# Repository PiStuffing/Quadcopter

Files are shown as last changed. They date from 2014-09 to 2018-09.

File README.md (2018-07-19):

Quadcopter
==========

Python project for an Raspberry Pi Autonomous Quadcopter Flight Controller

<a href="http://blog.pistuffing.co.uk/blog">Zoe flight</a>

Licensing
---------
<br />This work is licensed under a <a rel="license" href="http://creativecommons.org/licenses/by-nc-sa/4.0/">Creative Commons Attribution-NonCommercial-ShareAlike 4.0 International License</a>.

Index
-----
Documentation
<ul>
<li>README.md          - This file</li>
<li>LICENCE            - Usage definition</li>
<li>piDrones.pdf       - Documentation of piDrone details.</li>
</ul>
Code
<ul>
<li>piDrone            - Shell script driving qc.py with -O performance parameter
<li>qc.py              - Python wrapper allowing automatic use of the pre-compiled .pyc version of Quadcopter.py</li>
<li>Quadcopter.py      - Core flight controller code</li>
<li>RC.py              - Remote Control code</li>
</ul>
Flight plans
<ul>
<li>20s_hover_fp.csv   - Example simple flight plan CSV input file to hover a 1m</li>
<li>2m_square_fp.csv   - Example flight plan CSV input file to fly a 1m square 1m above the ground</li>
</ul>
Python libraries
<ul>
<li>RPIO.tgz           - clone of RPIO hardware PWM library (search GitHub for original)</li>
<li>smbus2.zip         - clone of I2C variount required for the RC joysticks (search GitHub for original)</li>
</ul>
PCBs
<ul>
<li>RPi0-PCB.brd       - Eagle board for Raspberry Pi 0 Quad</li>
<li>RPi3-PCB.brd       - Eagle board for Raspberry Pi 3 X8</li>
</ul>
Sensors
<ul>
<li>IMU_spec.pdf       - Invensense MPU-9250 specifications</li>
<li>GPS_spec.pdf       - u-blox NEO-M8T specification</li>
<li>Sweep_spec.pdf     - Scanse Sweep specification</li>
<li>LiDAR_spec.pdf     - Garmin LiDAR-Lite v3 specification</li>
<li>LiDARv3HP_spec.pdf - Garmin LiDAR-Lite v3HP specification</li>
<li>Joystick_spec.pdf  - Grayhill 67A specification</li>
</ul>

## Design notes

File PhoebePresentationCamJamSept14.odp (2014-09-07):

## Phoebe the Python Quadcopter

## Applications

- Professional Video
  - Countryfile
- Big Boys' Toys
  - Blooming Market
- Research Projects

## Demonstration

- Keep you expectations low!
  - 3 seconds take-off
  - 3 seconds hover
  - 3 seconds descent
  - autonomously
- Stand well back and be ready to run

## Hardware

- Props, Motors, ESCs, Frame off the shelf
- Raspberry Pi model A
- Custom PiBow + breadboard
- MPU6050 Sensor
- Velco, Blu-tack, Double-sided sticky tape

## Software

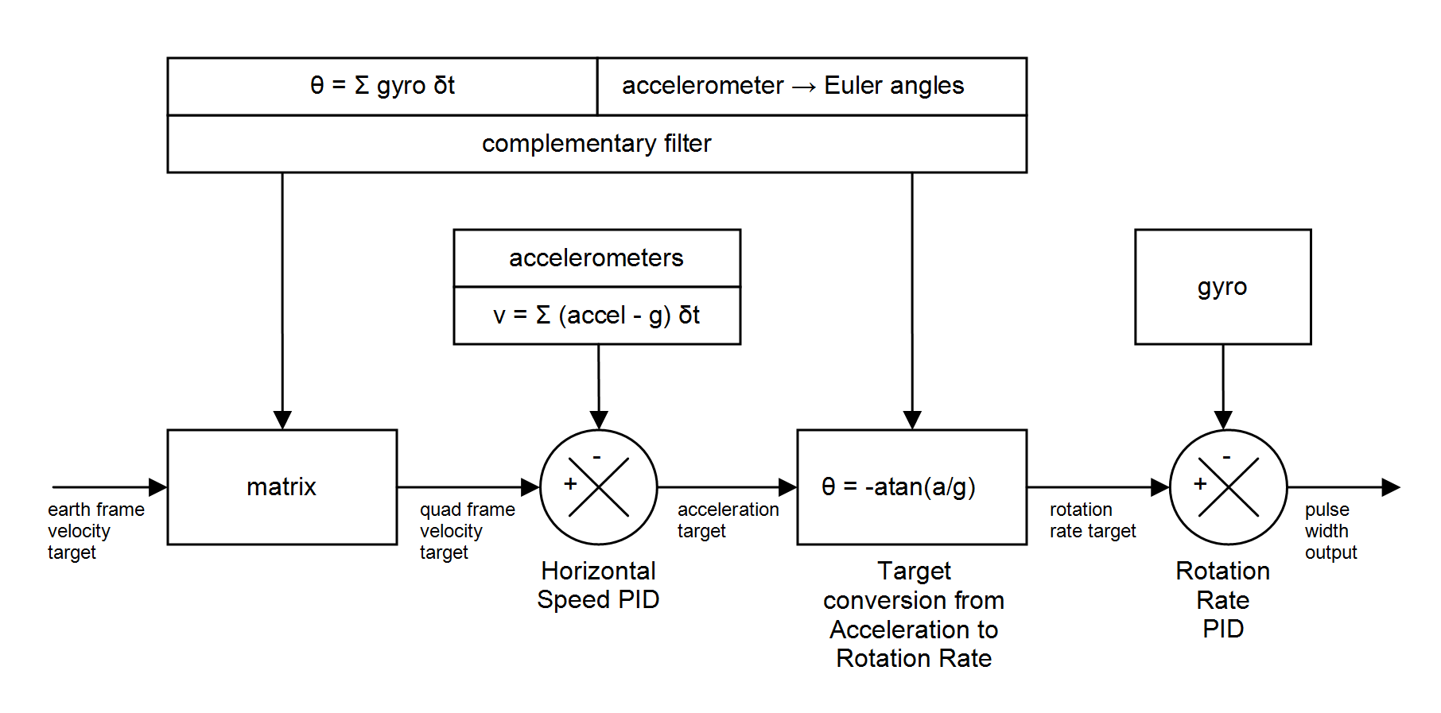
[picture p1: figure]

## Calibration

- Improve sensor accuracy
- Critical for velocity / gravity

## Performance

- Read sensors and integrate each loop
- Process results and feed @ 41Hz
- Performance 100Hz → 465Hz
  - I2C bus speed to 400kHz
  - MPU6050 data updates @ 1kHz
  - time.time()
  - GPIO interrupt
  - I2C read 1 x 14 bytes not 14 x 1 byte
  - GPU memory minimal
  - Code locked into memory

## What next?

- Physical rebuild
  - Frame
  - Motors, props, ESCs
- Sensors
  - Barometer / Altimeter
  - Magnetometer / Compass
  - GPS
- RaspiCam

## Any questions?

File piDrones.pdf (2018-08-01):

Master at https://github.com/PiStuffing/Quadcopter/blob/master/piDrones.pdf

# piDrones

## Version 1.0 – 1

## st August 2018

## Don’t Do It!

The aim of this documentation is to share details that could be interesting or useful for other projects. It lacks details about how to do your own DIY drone.

My target was to test the capabilities of me, a Raspberry Pi and python. I chose creating a piDrone not as a flying machine as such, but as an intellectual challenge requiring hardware, software and electronics.

My DIY piDrones has cost me £20k+ of research, development and testing over 6 years. Even building a DIY drone based on the instructions below will cost >£1.5k yet it supports (a little) less than a professional drone costing less than £1k.

If you want a flying machine, just buy a DJI Mavic or Spark and get out there flying.

However, if you want to know how flying machines work, read on…

## Internet Media

There are various links if you’re interested:

- pistuffing.co.uk has everything done over 6 years including non-drone projects and even non-Raspberry Pi projects
- pidrone.io/blog links to only drone posts
- pidrone.io/video links to only the videos
- pidrone.io/posts/xxx links to specific xxx posts for twitter
- vimeo.com/pistuffing covers all videos directly.

## Legal Constraint

The project, defined by the GitHub pistuffing/Quadcopter content, is for non-commercial usage. If you want to use this project commercially, contact me via andy@pistuffing.co.uk and let’s talk. After all, any financial compensation would be gratefully received!

Obviously, I’ll happily accept voluntary donations from anyone at http://blog.pistuffing.co.uk/donations/ 😊

## Raspberry Pis

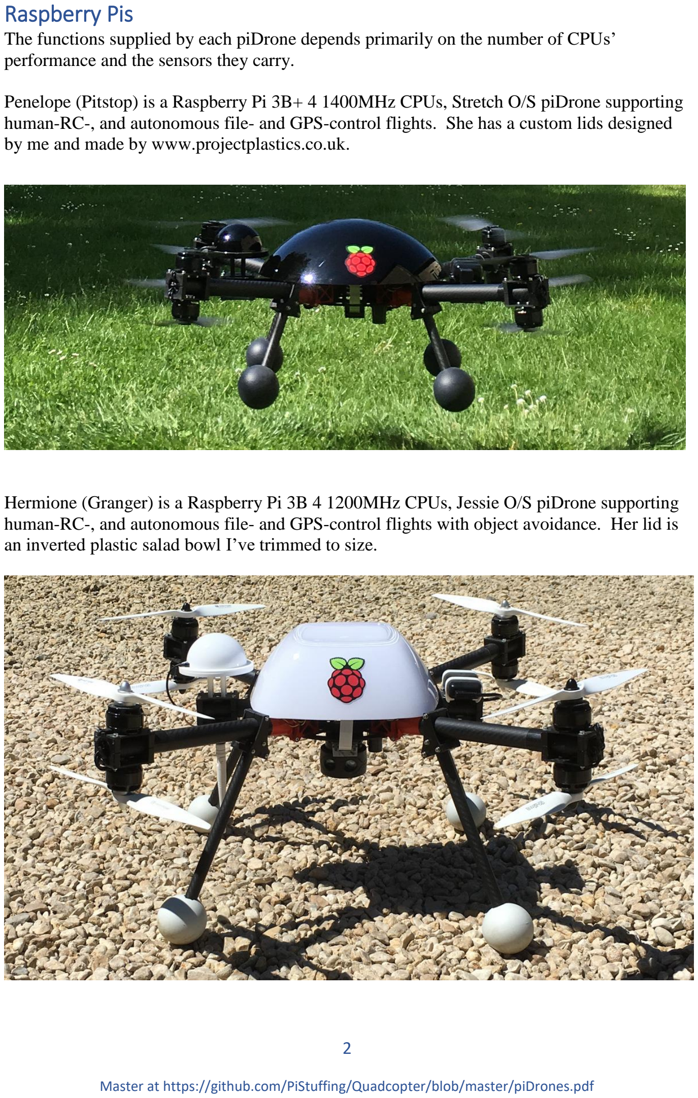
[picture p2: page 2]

The functions supplied by each piDrone depends primarily on the number of CPUs’ performance and the sensors they carry.

Penelope (Pitstop) is a Raspberry Pi 3B+ 4 1400MHz CPUs, Stretch O/S piDrone supporting human-RC-, and autonomous file- and GPS-control flights. She has a custom lids designed by me and made by www.projectplastics.co.uk.

Hermione (Granger) is a Raspberry Pi 3B 4 1200MHz CPUs, Jessie O/S piDrone supporting human-RC-, and autonomous file- and GPS-control flights with object avoidance. Her lid is an inverted plastic salad bowl I’ve trimmed to size.

Zoë (Johnny Ball’s daughter) is a Raspberry Pi0W single CPU, Stretch O/S piDrone supporting human-RC-, and file-control flights. She has a DIY lid with two 100mm clear dome and a tube from www.projectplastics.co.uk via ebay and joined, cut and painter myself.

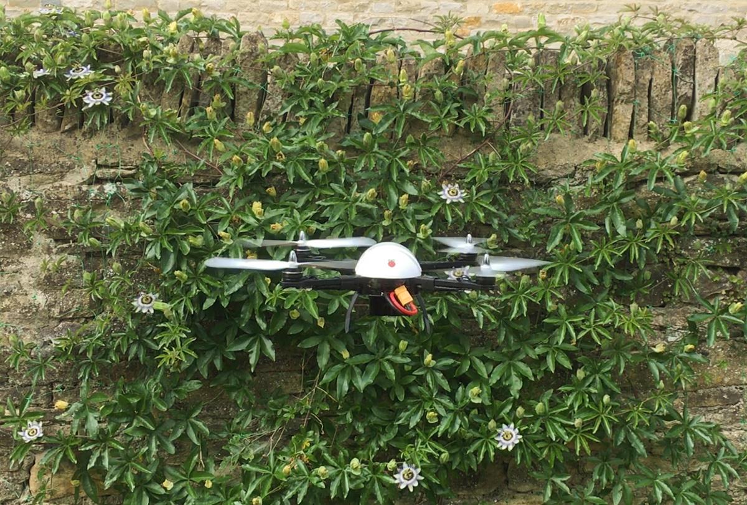
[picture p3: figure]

The piDrones’ naming convention is female (like ships and ‘planes) and end with a phonetic ‘-ee’. No ideas why for the latter, it just emerged. Phoebe was my first, Chloë the second, both of whom sadly are deceased.

Ivy is a Raspberry Pi B3+ Stretch piDrone supporting the human RC (remote control). A B3+ is not necessary, it’s only used as it was lying around unused. The case if a standard Ninja Pibow from pimoroni.com with a few custom extra layers to increase her thickness to include the joysticks.

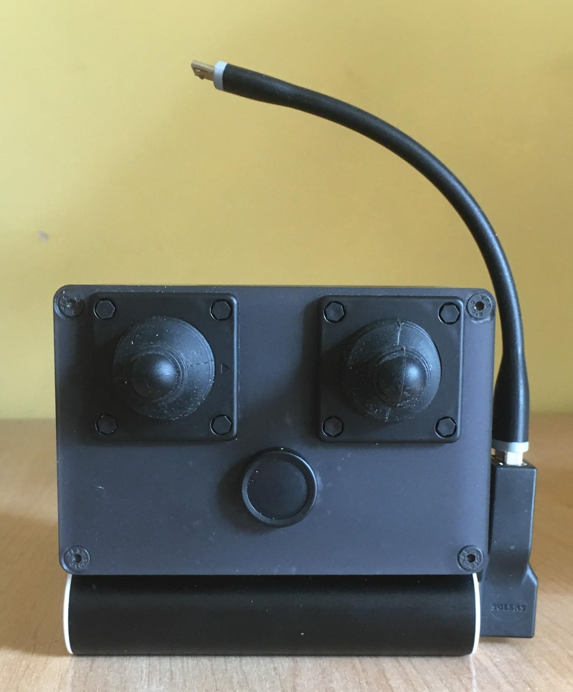
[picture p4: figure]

A fourth Raspberry Pi, piPad, is required to remote login to the piDrones (Penelope. Hermione or Zoë) and RC (Ivy) for control their executable. It’s a standard Raspberry Pi case + screen.

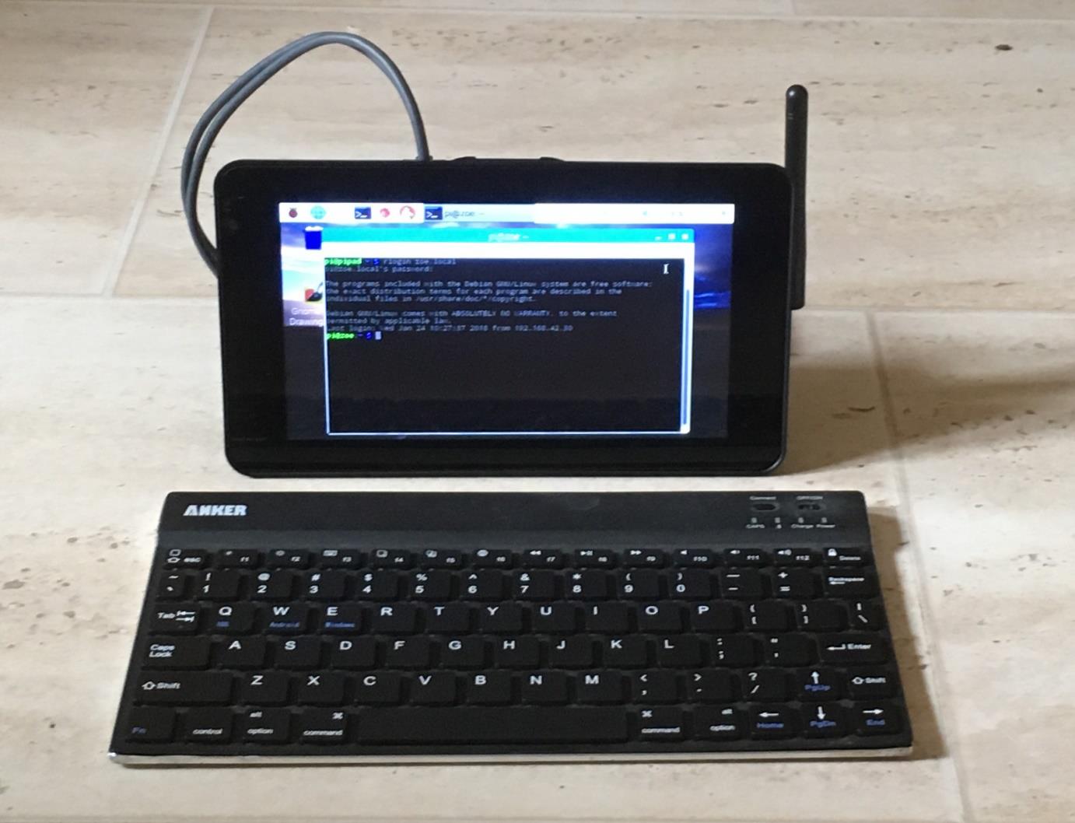
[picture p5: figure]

## Hardware

The hardware frames are no longer available. You’ll have to find your own.

Penelope uses eight T-motor CF 13x4.4 props, U3 KV700 motor and Air 40A ESCs, all available from electricwingman.com. Her frame is 75cm diagonally.

Hermione uses eight T-motor wooden 12x4.7 props (unavailable), U3 KV700 motor and Air 40A ESCs available from electricwingman.com. Her frame is 75cm diagonally.

Zoë uses four T-motor CF antiGravity! 9x3 props (unavailable), Air 2005/2000KV motors (unavailable) and Air 15A ESCs available from electricwingman.com. Her frame is 40cm diagonally.

## Power

LiPo batteries are explosive if shorted or damaged. Treat them with utmost respect.

Hermione and Penelope have two power sources: a 5V 2A battery bank for the Raspberry Pi and sensors, and a 4S1P (four series, 1 parallel) 14.8V (nominal) 6600mAh power LiPo batteries.

Zoë has just the 3S1P (three series, one parallel), 11.1V (nominal), 2300mAh power LiPo battery, along with a 5V 2A voltage regulator to run the Raspberry Pi and sensors. There is an internal switch to run just the Raspberry Pi and sensors to passive testing.

## Sensors

Here’s the list of sensors used:

- Inversense MPU-9250 IMU is for the accelerometer, gyrometer and magnetomer sensors and is available from pimoroni.com
- Garmin LiDAR-Lite v3HP is for the ground-facing vertical distance tracking and is available from robotshop.com
- RPi camera is for ground-facing lateral distance tracking and is available from pimoroni.com
- u-blox NEO-M8T is for GPS tracking and is available from drotek.com.
- Grayhill 67a is for RC joysticks and is available from avnet.com.
- ABI-009-RC buzzer is available from uk.farnell.com.
- IRLD024PBF MOSFET is for the beeper-switching and is available from uk.farnell.com.
- RECON R_78D5.0-2.0 5V 2A power supply is available from uk.farnell.com.
- Schurten MCS 18 switch is the button for the RC and is available from uk.farnell.com.

## PCBs

Eagle (autodesk.com – free use for individuals) is used to generate the CAM files required by ragworm.eu to generated the PCBs. They are available on GitHub/com/pistuffing/quadcopter/ as the following brd (board) files.

RPi3-PCB.brd is for a Raspberry Pi 3 supporting 4 or 8 motors. The IMU is on the middle with eight ESC connection sockets. The Garmin LiDAR-Lite v3HP is bottom center with 5v and output pins either side for constant and switchable 5V outputs respectively. The latter is currently used for the beeper.

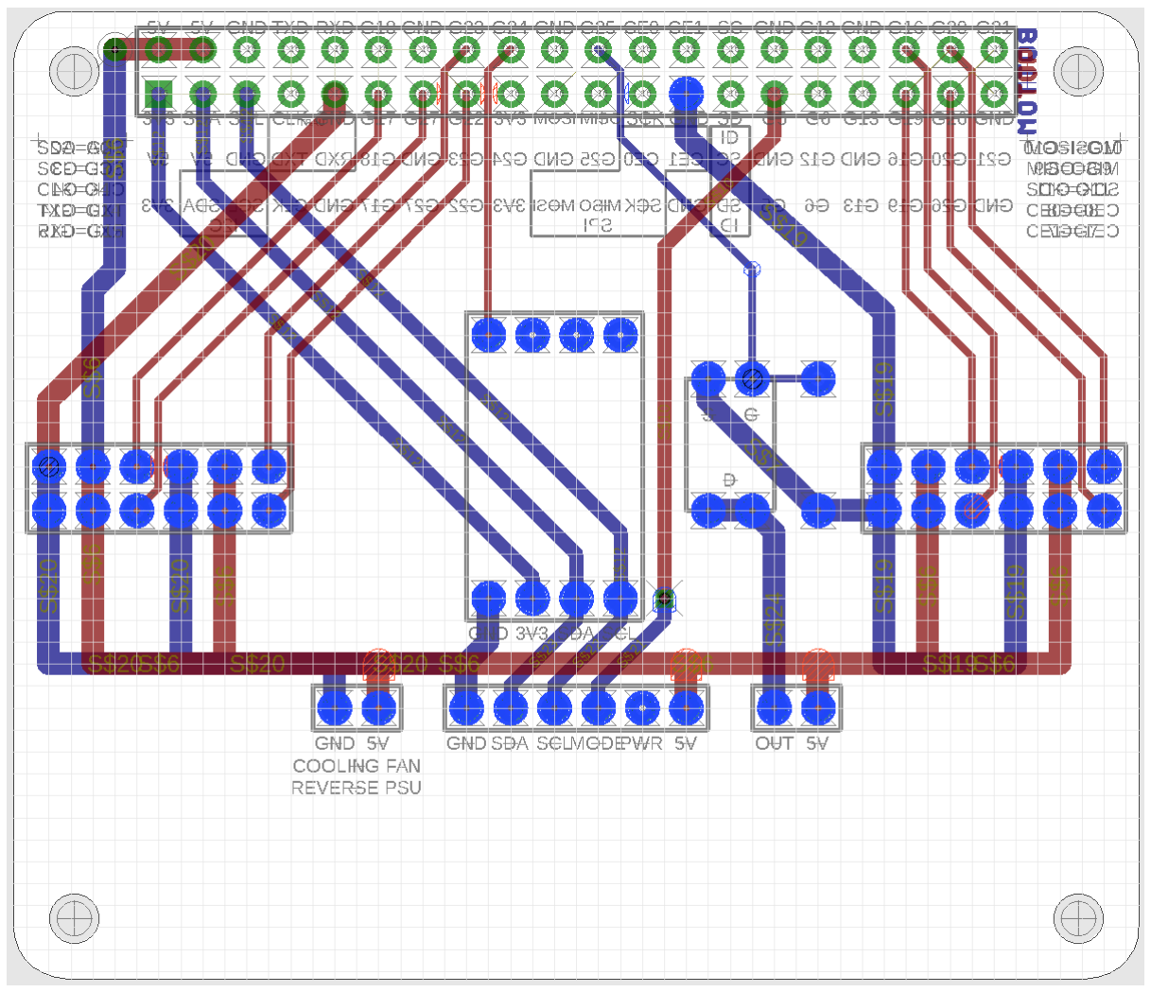
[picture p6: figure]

RPi0-PCB.brd is for a Raspberry Pi0W supporting 4 motors. The IMU is on the middle with four ESC connection sockets. The Garmin LiDAR-Lite v3HP connection is to the right with the 5V regulator at the left.

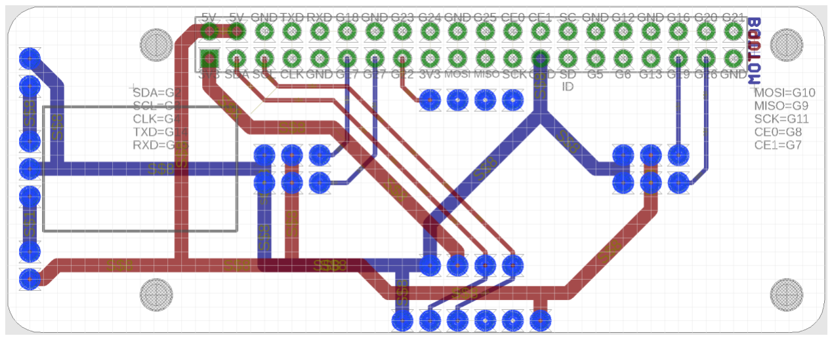
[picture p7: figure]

## Math(s)

I found this article useful reminding me of long forgotten trigonometry and rotational matrices: https://scholarsarchive.byu.edu/cgi/viewcontent.cgi?article=2324&context=facpub

## Processes

This is the five process layout for an autonomous system:

+—————+
|Sweep|———>———+
+—————+ | |
| +—————+———+ | +——————+
|Autopilot|——>——|Motion|
| +—————+———+ | +———+——+
+———+ | | | |
|GPS|————>————+ | |
+———+ | | |
+—————+ | |
| | |Video|——>——+
+—————+

This is the two process layout for a human-RC system:

+—————+
| | RC |······
+—————+ | ·
·
·
·
+———+——+
|Motion|
+———+——+
+—————+ | |
|Video|——>——+
+—————+

The difference is defined by the code constants autopilot_installed or rc_installed. The Pi0W is only capable of the latter due to the single CPU.

## Code

The code is a single file, Quadcopter.py. It’s ‘self-documenting’, split into

- 1700 comments
- 900 blanks
- 2700 lines of code.

The code structure from top to bottom is:

- I

2C
- Sensors
- PIDs / ESCs
- Trigonometric and rotation matrices
- Control function
- *Process & *Manager pair control process management
- class Quadcopter().

The code lives at https://github.com/PiStuffing/Quadcopter/blob/master/Quadcopter.py. In “class Quadcopter():”, start at “while self.keep_looping:” in “def fly()” which runs the flight itself; dig in the details from there.

## ESCs

Electronic speed controllers (?) are the firmware units which translate from Raspberry Pi PWM signals to the power from the motors. The PWM signal is from 1000us to 2000us signals with 1us resolution, signaled up to 500Hz. For this reason, software PWM is insufficient as supplied by RPi.GPI and instead, the PWM python module RPIO must be used.

1000us pulses synchronize with the motors and stops them whining.
1150us pulses starts the motors at minimum rotation rate.
1500us pulses are approximate the hover value.
1999us pulses at full speed.

The middle pair listed above require tuning based on the ESCs and motors used.

## Installation

### Basic Confirguration

- Use Etcher (https://etcher.io/) to write the SD card with the latest Raspian Lite (https://www.raspberrypi.org/downloads/raspbian/) image
- In windows in the root directory of the SD card, create an SSH file to enable it

echo hello > ssh

- Boot up your RPi with SD card, keyboard, mouse, monitor and WAP / soft AP supporting WiFi dongle installed (no WiFi dongle needed for 3B and Zero-W)
- Sudo raspi-config to set hostname, GPU memory (128MB), enable I²C, overclock to 1GHz, disable overscan, disable serial UART, enable camera support and SSH server. Do this incrementally to make sure each change takes effect in /boot/config.txt
- sudo apt-get update
- sudo apt-get dist-upgrade
- sudo apt-get install i2c-tools python-smbus python-dev python-setuptools python-picamera python-gps python-serial git ftp
- edit /boot/config.txt adding

dtparam=i2c_arm_baudrate=400000

- while in /boot/config.txt, disable pointless functions thus

dtparam=audio=off
start_x=0
- If you are using a Pi3 or Zero-W, you may want to disable Bluetooth in /etc/modprobe.d/raspi-blacklist.conf thus:

# WiFi

# blacklist brcmfmac

# blacklist brcmutil

# Bluetooth

blacklist btbcm
blacklist hci_uart

Likewise if you're using an WiFi USB dongle, you can disable the internal one by removing the '#'s for that pair of lines.

- If you are using a Raspberry Pi 2 B V1.2, it can be overclocked to 1.2GHz thus in /boot/config.txt

arm_freq=1200
core_freq=500
sdram_freq=600
force_turbo=1
over_voltage=6
- If you are using multiple USB UART devices (i.e. GPS and Scanse Sweep in Hermione’s case), it's necessary to link the USB /dev/ttyUSB* to a unique name for each. In /etc/udev/rules.d add a file such as '99-usb-serial.rules containing something like this:

SUBSYSTEM=="tty", ATTRS{idVendor}=="0403", ATTRS{idProduct}=="6015", ATTRS{serial}=="DO004VY5", SYMLINK+="ttySWEEP"
SUBSYSTEM=="tty", ATTRS{idVendor}=="067b", ATTRS{idProduct}=="2303", SYMLINK+="ttyGPS"

The details of what to fill in come from /var/log/messages as a USB UART is plugged in. Also /etc/default/gpsd and Quadcopter.py to reference these tty* names instead of ttyUSB*. More details here: http://hintshop.ludvig.co.nz/show/persistent-names-usb-serial-devices/

- Add hardware PWM

git clone -b v2 https://github.com/metachris/RPIO
cd RPIO

check mailbox.c code exists in source/c_pwm/mailbox.c to conform you have the right version, then install thus

sudo python ./setup.py install
cd ~
- Add I²C variant for RC joysticks

git clone https://github.com/kplindegaard/smbus2 cd smbus2
sudo python ./setup.py install
cd ~
- Add Quadcopter code

git clone https://github.com/PiStuffing/Quadcopter cp Quadcopter/qc.py .
cp Quadcopter/pidrone .

cp Quadcopter/fp.csv .
cp Quadcopter/Quadcopter.py .
cd ~

### Wireless Access Point Network Configuration

This is based on https://www.raspberrypi.org/documentation/configuration/wireless/access-point.md.

Install required software elements:

- sudo apt-get install dnsmasq hostapd
- sudo systemctl stop hostapd
- sudo systemctl stop dnsmasq

Set up the static IP address:

- sudo vi /etc/dhcpcd.conf

interface wlan0
static ip_address=192.168.42.1/24
- sudo service dhcpcd restart
- sudo mv /etc/dnsmasq.conf /etc/dnsmasq.conf.org
- sudo vi /etc/dnsmasq.conf

interface=wlan0
usually wlan0
dhcp-range=192.168.42.2,192.168.42.20,255.255.255.0,24h

Set up the access point:

- sudo vi /etc/hostapd/hostapd.conf

interface=wlan0
driver=nl80211
ssid=HoGWAP
channel=1
wmm_enabled=0
wpa=1
wpa_passphrase=HoG3.141592654 wpa_key_mgmt=WPA-PSK
wpa_pairwise=TKIP
rsn_pairwise=CCMP
auth_algs=1
macaddr_acl=0

Enable hostapd:

- sudo vi /etc/default/hostapd

DAEMON_CONF=”/etc/hostapd/hostapd.conf”

Comment out any ”NETWORK={” in /etc/wpa_wpa_supplicant/wpa_supplicant.conf.

Edit /etc/hostname to ensure the domain name is included - in my case, the domain is called local, and the hostname is pidrone, so /etc/hosts reads

- pidrone.local

Next assign static IP address for the piDrone, where pidrone is zoe, hermione or penelope.

- sudo vi /etc/hosts

127.0.1.1 pidrone.local
192.168.42.1 pidrone.local pidrone

Check, double check, and triple check that you've done all the above steps, and then finally

- sudo reboot

To backout temporarily to allow for O/S updates etc

- sudo vi /etc/default/hostapd

DAEMON_CONF=””

- Reinstate any “NETWORK={“ enties in /etc/wpa_supplicant/wpa_supplicant.conf
- Comment out the AP interface IP details in /etc/dhcpcd.conf
- reboot

## Flights

Run the piDrone with the main command-line sh script:

./piDrone

This enforces python optimization thus:

sudo python -O ./qc.py

This then calls the library Quadcopter.py. The method means the library with actually run the optimized Quadcopter.pyo if available.

The following are the primary commands; fine tuning parameters are available.

### Initial Setup

--tc 1 -h 1150 turns each blade one by one so you can check all are working, and are rotate the connect direction. My code assumes the top front left prop is anti- (counter-) clockwise.

-d diagnostics logged to qcstats.csv which when fed into a spreadsheet (e.g. Excel) can show graphs about all key parameters from sensors and resultant actions.

--cc checks or calibrates magnetometer i.e. a 3D compass

### Autonomous File Flight Control

-f flightplanfile

The flightplanfile is based on a series of lines like this while flies on a horizontal square. Takeoff and landing are automatic:

# - evx is fore / aft velocity in m/s; fore is positive

# - evy is port / starboard velocity in m/s; port is positive

# - evz is up / down velocity in m/s; up is positive

# - time is how long to maintain that speed in seconds

# - name is an arbitrary name put out to console to show flight progress

# evx, evy, evz, time, name

0.0, | 0.0, | 0.0, | 1.0, HOVER
0.25, 0.0, | 0.0, | 4.0, FORE
0.0, | 0.0, | 0.0, | 1.0, HOVER
0.0, 0.25, | 0.0, | 4.0, PORT
0.0, | 0.0, | 0.0, | 1.0, HOVER
-0.25, 0.0, | 0.0, | 4.0, AFT
0.0, | 0.0, | 0.0, | 1.0, HOVER
0.0,-0.25, | 0.0, | 4.0, STARBOARD
0.0, | 0.0, | 0.0, | 1.

### Autonomous GPS Flight Control

--cwp – clear previous set of GPS waypoints
--awp – add another GPS waypoint to the list
--gps – fly from an arbitrary take-off locations to the series of preset waypoints in turn

### Manual File Flight Control

-f flight_plan

The manual, pre-written “flight_plan” file contains a series of lines, each of which define lateral and vertical velocities, along with time spam and name. In the example below, this results on a two meter square horizontal flight over twenty one seconds.

Takeoff and landing are automatic:

# - evx is fore / aft velocity in m/s; fore is positive

# - evy is port / starboard velocity in m/s; port is positive

# - evz is up / down velocity in m/s; up is positive

# - time is how long to maintain that speed in seconds

# - name is an arbitrary name put out to console to show flight progress # evx, evy, evz, time, name

0.0, | 0.0, | 0.0, | 1.0, HOVER
0.25, 0.0, | 0.0, | 4.0, FORE
0.0, | 0.0, | 0.0, | 1.0, HOVER
0.0, 0.25, | 0.0, | 4.0, PORT
0.0, | 0.0, | 0.0, | 1.0, HOVER
-0.25, 0.0, | 0.0, | 4.0, AFT
0.0, | 0.0, | 0.0, | 1.0, HOVER
0.0,-0.25, | 0.0, | 4.0, STARBOARD
0.0, | 0.0, | 0.0, | 1.0, HOVER

### Manual RC Flight Control

--rc

The piDrone is booted up first to establish the WAP. They the RC and control RPi are booted, and connected to the piDrone WiFi. From in the control RPi, via a pair of terminal windows, rlogin to the piDrone and the RC. Start the piDrone (./pidrone) and the RC (python ./RC.py). When you type in “—rr” on the piDrone command line, the RC and piDrone connect, and an auto-takeoff takes place. Thereafter, the RC is under your control. To trigger an auto-landing, push the joysticks inwards towards each other until the landing is initiated; the landing height is also automated.

## What next?

Any further development is primarily restricted by WiFi and battery constraints: WiFi range is 40m maximum, and for the larger models, batteries last a few minutes maximum; without these resolved, nothing further is possible.

Assuming those could be resolves, then:

- include higher resolution video lateral tracking with a future version of the Raspberry Pi – there’s a balance between IMU and Video processing; the two need to be in sync – more CPU speed would allow higher Video resolution without a synchronization hit
- long distance flights with a 2nd camera for taking photos / video
- fuse GPS with IMU and LiDAR / Video for lateral and vertical measurement when unavailable for current set e.g. flying over a lake or altitude high than range of the LiDAR.

Fundamentally though, that ain’t gonna happen without the primary constraints resolved, hence this is the end on of this project for now.

“So long, and thanks for all the fish!”

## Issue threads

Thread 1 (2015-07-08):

Provide the schematics as a pdf file too

Nolaan, 2015-07-08:
Hi,
It would be great if the schematics were available in pdf format. Thanks

PiStuffing, 2015-07-08:
I don't have schematics, sorry.  The PCB is a simple breadboard which I wired up to meet the code I'd already written.  See here for what the wiring layout was - the nearest to a schematic I have:

http://blog.pistuffing.co.uk/byoaq-bat-i-assembly-electronics/

Hollys48, 2015-07-08:
Hi, some how the link has sent this email to me, I have nothing to do with
this or any knowledge.

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

Closed 2015-07-08.

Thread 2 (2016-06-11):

Resources?

nathanpelt, 2016-06-11:
Hi this is Nathan. I have a few questions regarding your raspberry pi quad-rotor. What development environment did you use to write your code? I looked over your pdf but it did not mention any development environment. Also if you would have any names or links to resources or books on writing embedded code like your python i2c code that would be great.  I know how to program in a few languages but really haven't done any embedded development before. Thanks for your time.

PiStuffing, 2016-06-11:
Hi Nathan,

I didn't use a development environment - python is such an easy language to write that I just wrote the code in a text editor, and ran it to test it.  Because a Raspberry Pi is a true linux computer rather than an embedded system like an Arduino, there's no need for a separate computer to cross-complile / load the code.  Everything can be done on the RPi.

The basic I2C code at the top of Quadcopter.py came from an example from adafruit: https://learn.adafruit.com/adafruit-16-channel-servo-driver-with-raspberry-pi/overview.  I then added calls to it to add error protection and higher performance.  There is a python library (python-smbus in the Raspian distribution) that does most of the work, and my code just calls the various read and write calls provided by the smbus library.

Hope that helps,

Andy

Closed 2016-06-12.

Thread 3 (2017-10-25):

Regarding orientation of sensors.

jovinjijo, 2017-10-25:
Reading through the documentation and code, I couldn't find how the sensors (MPU6050 and Compass) should be fixed.
Is there a default orientation? If yes, can it be changed? Is it hard coded in the python script?
Any help would be great.

PiStuffing, 2017-10-25:
Take a look here: http://blog.pistuffing.co.uk/wp-content/uploads/2017/05/DSC01347.jpg

I use the Sparkfun MPU-9250 breakout.  It's in the middle of the PCB in the picture from the link.  The accelerometer X axis points "forwards" from the drone point of view (i.e. leftwards pointing in the picture), y axis points left from drone POV (downwards in the picture), and Z axis upwards (towards the camera in the picture).  This is what the python is coded to match.

The easiest way to change this orientation would be in readFIFO().  This is the deepest point where the code assigns X forwards, Y left, Z up and names the FIFO register contents that way.  So that's the point you could allow for the MPU9250 X register to actually be "right" for example.

jovinjijo, 2017-10-26:
Okay. That was really helpful.
Thank you.

Closed 2017-10-26.

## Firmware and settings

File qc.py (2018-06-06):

#!/usr/bin/env python

###############################################################################################
###############################################################################################
##                                                                                           ##
## Hove's Raspberry Pi Python Quadcopter Flight Controller.  Open Source @ GitHub            ##
## PiStuffing/Quadcopter under GPL for non-commercial application.  Any code derived from    ##
## this should retain this copyright comment.                                                ##
##                                                                                           ##
## Copyright 2014 - 2018 Andy Baker (Hove) - andy@pistuffing.co.uk                           ##
##                                                                                           ##
###############################################################################################
###############################################################################################

from Quadcopter import Quadcopter
import os

os.nice(-10)

if __name__ == '__main__':
	#-------------------------------------------------------------------------------------
	# Off we go!
	#-------------------------------------------------------------------------------------
	Quadcopter().go()

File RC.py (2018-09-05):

#!/usr/bin/python

####################################################################################################
####################################################################################################
##                                                                                                ##
## Hove's Raspberry Pi Python Quadcopter Flight Controller.  Open Source @ GitHub                 ##
## PiStuffing/Quadcopter under GPL for non-commercial application.  Any code derived from         ##
## this should retain this copyright comment.                                                     ##
##                                                                                                ##
## Copyright 2012 - 2018 Andy Baker (Hove) - andy@pistuffing.co.uk                                ##
##                                                                                                ##
####################################################################################################
####################################################################################################

from __future__ import division
from smbus2 import SMBusWrapper, i2c_msg
import math
import socket
import struct
import sys
import select
import time
import RPi.GPIO as GPIO


def client():

    ################################################################################################
    #                              MAKE CONNECTION TO SERVER
    ################################################################################################

    poll = select.poll()

    go_go_go = False

    pack_format = "=ffffb?"
    pack_size = struct.calcsize(pack_format)

    unpack_format = "=?"
    unpack_size = struct.calcsize(unpack_format)

    client = socket.socket()
    addr = "192.168.42.1"
    port = 31415

    '''
    client_fd = client.fileno()
    poll.register(client_fd, select.POLLIN | select.POLLPRI)
    '''

    ################################################################################################
    #                                  SET UP THE JOYSTICKS FSM
    ################################################################################################

    RC_PASSIVE = 0
    RC_TAKEOFF = 1
    RC_FLYING = 2
    RC_LANDING = 3
    RC_DONE = 4
    RC_ABORT = 5

    state_name = ["PASSIVE", "TAKEOFF", "FLYING", "LANDING", "DONE", "ABORT"]

    status_quo = [0.0, 0.0, 0.0, 0.0]

    #-----------------------------------------------------------------------------------------------
    # Set up GPIO for button and buzzer
    #-----------------------------------------------------------------------------------------------
    GPIO.setmode(GPIO.BCM)

    GPIO_BUTTON = 10
    GPIO.setup(GPIO_BUTTON, GPIO.IN, GPIO.PUD_DOWN) # GPIO button pushed pulls GPIO high

    GPIO_BUZZER = 24
    GPIO.setup(GPIO_BUZZER, GPIO.OUT) # GPIO buzzer set high sounds the buzzer
    GPIO.output(GPIO_BUZZER, GPIO.LOW)

    #-----------------------------------------------------------------------------------------------
    # Acquire contact with the piDrone; only continue below once acquired.
    #-----------------------------------------------------------------------------------------------

    with SMBusWrapper(1) as bus:
        try:
            while True:

                #-----------------------------------------------------------------------------------
                # Connect to the server
                #-----------------------------------------------------------------------------------
                print "CONNECTING..."
                while True:
                    try:
                        client.connect((addr, port))
                    except:
                        time.sleep(0.1)
                    else:
                        break
                print "CONNECTED."        

                #-----------------------------------------------------------------------------------
                # We are connected to the piDrone.
                #-----------------------------------------------------------------------------------
                client_fd = client.fileno()
                poll.register(client_fd, select.POLLIN | select.POLLPRI)
                connected = True

                #-----------------------------------------------------------------------------------
                # Wait for a piDrone status update for go / stop
                #-----------------------------------------------------------------------------------
                go_go_go = False
                while connected:

                    ################################################################################
                    #                        HANDLE MESSAGES FROM THE SERVER
                    ################################################################################

                    #-------------------------------------------------------------------------------
                    # Sleep pending an input for the piDrone 
                    #-------------------------------------------------------------------------------
                    results = poll.poll(200) # milliseconds

                    #-------------------------------------------------------------------------------
                    # Check whether there's I/O from RC
                    #-------------------------------------------------------------------------------
                    for fd, event in results:
                        assert fd == client_fd, "WTF HAPPENED HERE"

                        #---------------------------------------------------------------------------
                        # Has piDrone told piRC to start?
                        #---------------------------------------------------------------------------
                        raw = client.recv(unpack_size)
                        assert (len(raw) == unpack_size), "Invalid data"

                        #---------------------------------------------------------------------------
                        # React on the action from the message from the piDrone
                        #---------------------------------------------------------------------------
                        formatted = struct.unpack(unpack_format, raw)

                        if formatted[0]: # is True
                            GPIO.add_event_detect(GPIO_BUTTON, GPIO.FALLING)

                            #-----------------------------------------------------------------------
                            # piDrone is connected, start the flight
                            #-----------------------------------------------------------------------
                            go_go_go = True
                            state = RC_TAKEOFF
                            takeoff_time = time.time()

                            print "GO GO GO"
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

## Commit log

2013-12-10 PID tuning for take-off and drift
    [qc.py]
2014-06-05 assortment of minor fixes and enhancements
    [qc.py]
2014-06-05 Minor bugs crept into last update
    [qc.py]
2014-06-11 Noise reduction for acceleration to angle code
    [qc.py]
2014-07-12 Changes to reference frames, timing, PIDs and averaging
2014-08-13 Radical rework of internal processing / calibration
    [qc.py]
2014-09-07 Performance enhanced GPIO library for interrupts f Please enter the commit message for your changes. Lines s
2014-09-12 Eagle layout for B+ breadboard PCB
    [beret.brd]
2014-11-09 Complimentary filter bug
2014-11-24 Rolling averaging of accelerometer
2014-12-06 Rework so bulk of code runs as bitcode from .pyc
    [qc.py]
2014-12-27 Complementary filter for Euler frames
2015-01-27 Layout out for DroTek 10 DOF IMU + tweaks
    [beret.brd]
2015-02-04 Gravity filtering and tuning
2015-02-14 Butterworth filtering for gravity
2015-04-16 PRotection from sensor error handling
    [qc.py]
2015-07-17 Fine tuning of timing, filters etc
2015-07-17 Updated customer GPIO library to track RPi.GPIO enhancements
2015-08-22 Example flight plan CSV file
    [fp.csv]
2015-08-22 Move flight plan to CSV file, and minor PID tuning
2015-10-23 Temperature and tidying
2015-12-17 Zoe the Zero PCB layout and gerbers
    [ZoeZeroEagle.brd]
2015-12-26 Quadcopter Data Ready Interrupt Code
2016-01-21 Quadcopter.py now uses the IMU FIFO
2016-01-21 Quadcopter.py now uses the IMU FIFO code
2016-01-25 Phoebe's A+ custom PCB
    [PhoebeHATEagle.brd]
2016-02-12 As good as it gets with just 2 sensors
2016-06-03 Add various sensors, error protection & performance
2016-12-18 Successful sensor fusion update
2017-01-10 General update to latest versions
    [A+X8Eagle.brd, ZoeZeroEagle.brd]
2017-03-27 Delete PhoebeHATEagle.brd
    Retired
    [PhoebeHATEagle.brd]
2017-03-27 Delete beret.brd
    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
    [beret.brd]
2017-03-27 Delete ZoeZeroEagle.brd
    Redundant duplicate
    [ZoeZeroEagle.brd]
2017-03-27 Delete A+X8Eagle.brd
    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
    [A+X8Eagle.brd]
2017-04-24 Update to latest tested level.
    [lfp.csv]
2017-05-04 Tidying and a fix for if the camera isn't installed.
2017-07-16 Add 'import Serial' for Scnase Sweep USB UART input.
2018-01-26 Yaw + fuse Hermione and Zoe
2018-01-26 Update flight flans
    [fp.csv, lfp.csv]
2018-04-28 Required for RC I2C
2018-04-28 RC i2C variant
2018-06-18 PCB detains
    [RPi0-PCB.brd, RPi3-PCB.brd]
2018-06-18 Replaced by RPi0-PCB.brd
2018-06-22 Tidying up.
    [RPi0-PCB.brd]
